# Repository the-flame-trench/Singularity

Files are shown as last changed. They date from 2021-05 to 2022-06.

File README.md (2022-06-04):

# Singularity On-board Computer
Singularity is a high-reliability focused on-board computer (OBC) for Pocketqube scale spacecraft.

It has been designed with a high degree of redundancy and fault tolerance in mind, and is compliant to ECSS-Q-ST-70-12C where possible.

# Design
The computer is based on the TI TMS570 family of safety critical microcontrollers, utilising dual lockstep ARM Cortex R4F CPU cores with extensive error checking capabilies.  

The rest of the board contains 8Mb external FRAM, 1Gb external bulk flash (both on their own single SPI bus), and a supervisor IC with RTC, watchdog and 256kb integrated FRAM (Issue_PROTO_A only).

Additionally, the board breaks out 3 CAN buses, with 1 designated for platform services, 1 for payload use, and a shared redundant bus.

As the Singularity OBC is being designed primarily for use in our TFTqube project, specific functions have been broken out to each connector, including a UART bus to a GPS module and a shared internal/external I2C bus.

The board is designed to be powered by a 3V3 external supply.  For maximum reliability, this supply should have some level of redundancy.  There is also a designated 5V input rail, although this is currently unused.

The board contains bulk decoupling for the main 3V3 rail, which is then distributed to various ICs.  The 3V3 rail is also fed through redundant TPS62850 switch mode power supplies, with outputs OR'd by an ideal diode controller and pair of MOSFETS, to provide a redundant 1V2 rail for the TMS570 core supply.

A version of the computer with 32MB SDRAM is under study, however at present, on an already dense 6 layer board, layout is infeasible.

# Usage
First, clone [TFT-KiCad-Source](https://github.com/the-flame-trench/TFT-KiCad-Source) and import all symbol and footprint libraries, found under /TFT_symbols and /TFT_footprints respectively, to your KiCad installation.  This MUST be done first, as the Singularity project references this library (as do other TFT projects).

Then, clone the Singularity repo, ensuring that your library tables are correctly set up with the TFT component libraries before opening the project.

# Contributing
The schematic and PCB are being designed in KiCad v6.0, and will move with the latest stable version.

We are working to bring every symbol and footprint into the TFT KiCad source libraries, however currently there are still a few instances using the default KiCad component library.

# Licence
Licenced under the [CERN OHLv2 - Strongly Reciprocal](LICENCE) or as referenced.

(c) The Flame Trench 2022

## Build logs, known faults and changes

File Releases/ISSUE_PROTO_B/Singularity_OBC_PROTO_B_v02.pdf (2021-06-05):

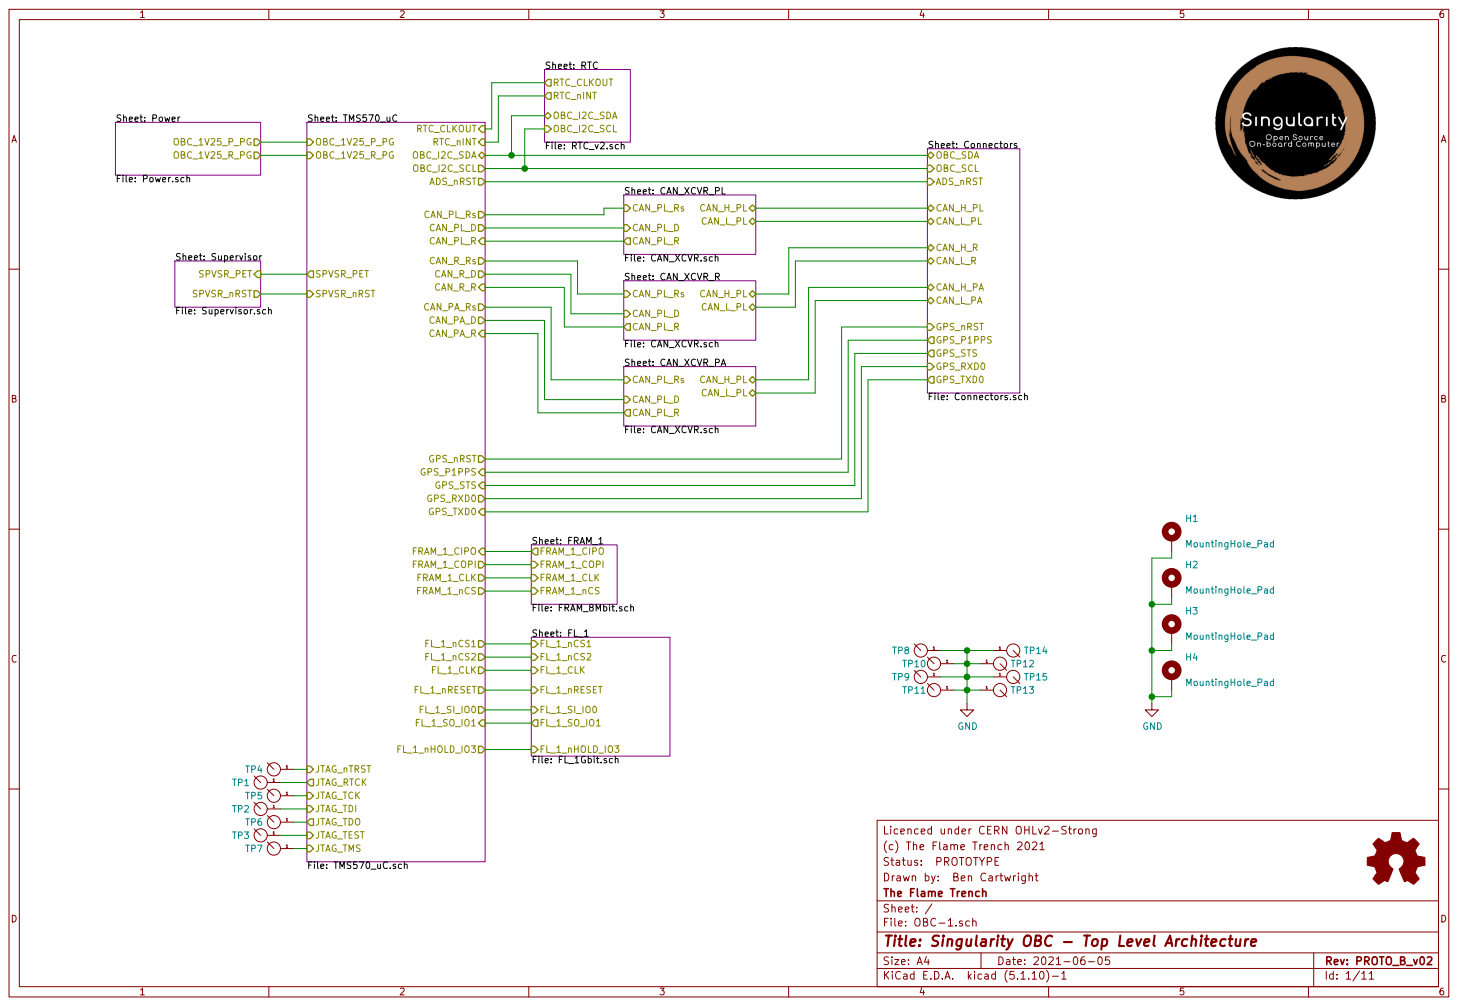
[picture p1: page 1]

File: RTC_v2.sch OBC_I2C_SDA OBC_I2C_SCL RTC_CLKOUT RTC_nINT Sheet: Power File: Power.schOBC_1V25_P_PG

Sheet: Connectors File: Connectors.sch OBC_SDA OBC_SCL ADS_nRST CAN_H_PL CAN_L_PL CAN_H_R

Licenced under CERN OHLv2-Strong
(c) The Flame Trench 2021
File: OBC-1.sch Sheet: / The Flame Trench Drawn by: Ben Cartwright Status: PROTOTYPE

Id: 1/11 Title: Singularity OBC - Top Level Architecture

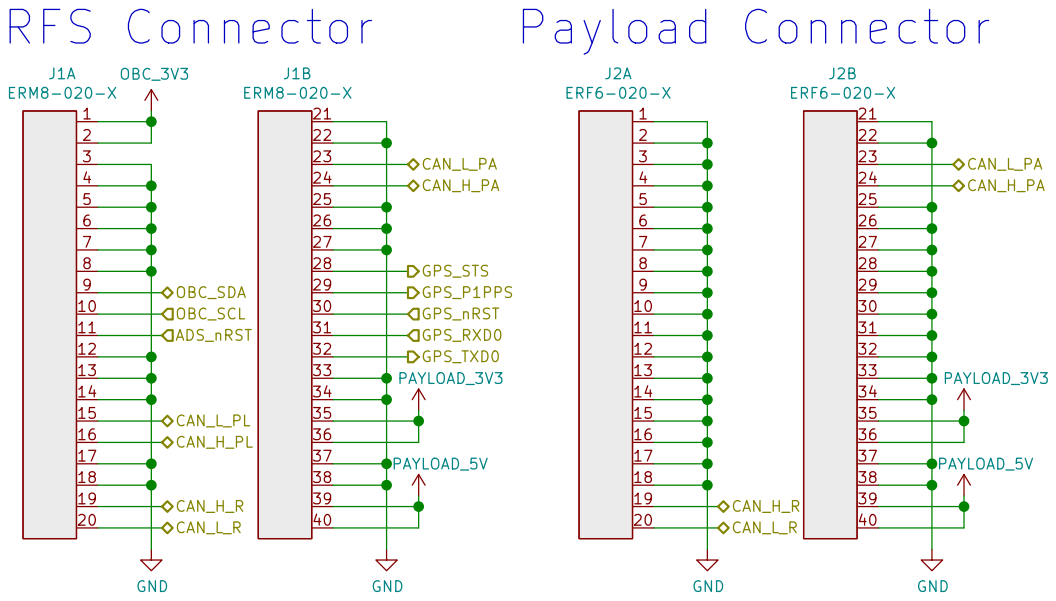
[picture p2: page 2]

Licenced under CERN OHLv2-Strong GND

(c) The Flame Trench 2021
File: Connectors.sch Sheet: /Connectors/ The Flame Trench Drawn by: Ben Cartwright Status: PROTOTYPE

Id: 2/11 Title: Singularity OBC - Connectors

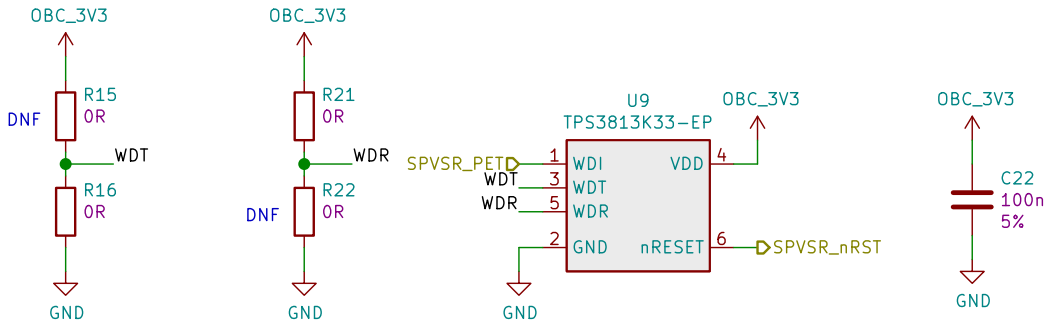
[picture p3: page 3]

Licenced under CERN OHLv2-Strong
(c) The Flame Trench 2021
Sheet: /Supervisor/ The Flame Trench Drawn by: Ben Cartwright Status: PROTOTYPE

File: Supervisor.sch
Id: 3/11 Title: Singularity OBC - Supervisor

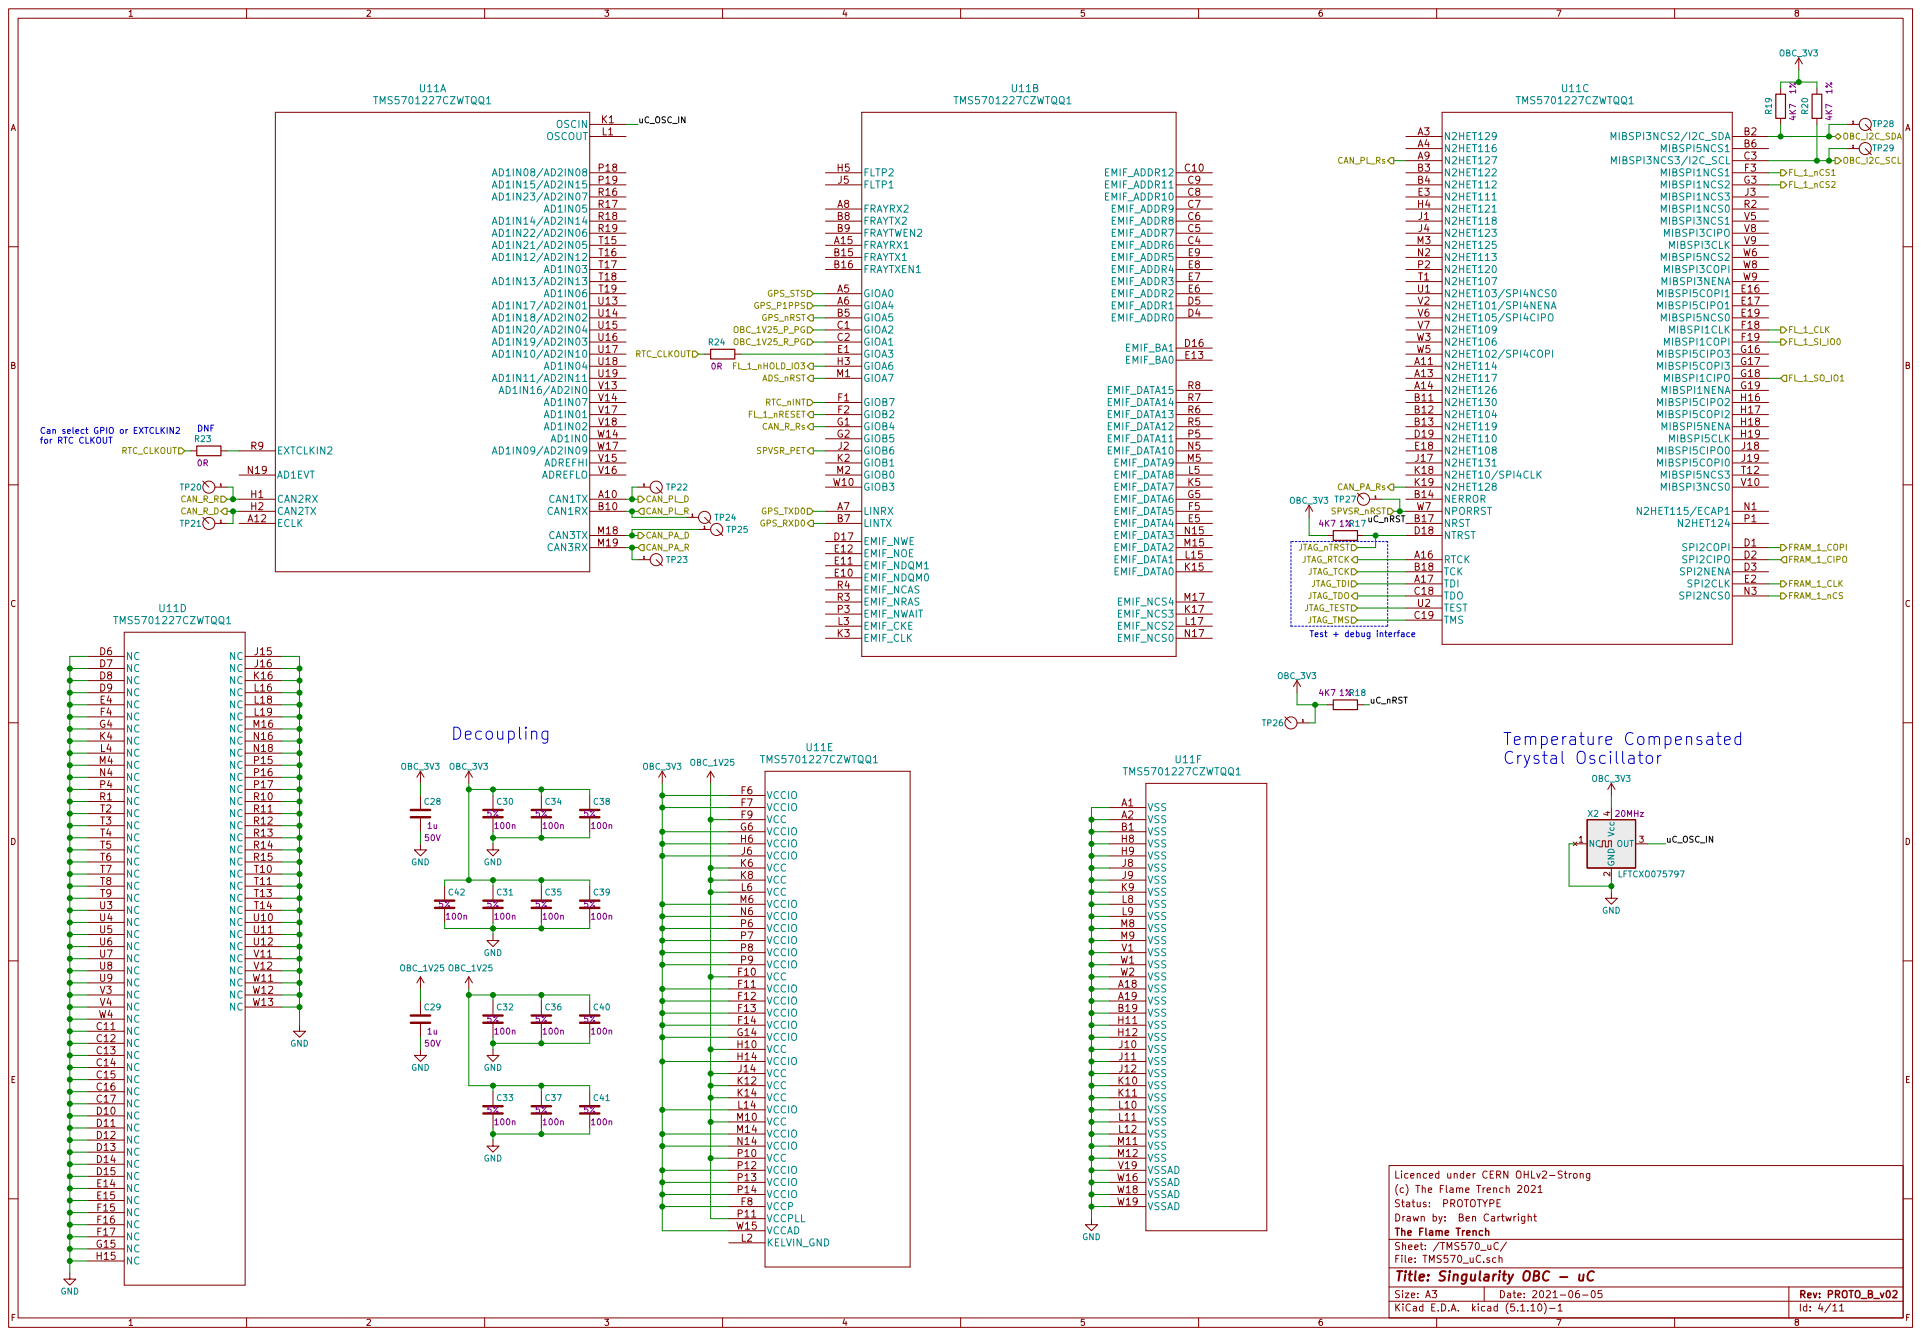
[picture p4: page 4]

Crystal Oscillator Can select GPIO or EXTCLKIN2
for RTC CLKOUT

Licenced under CERN OHLv2-Strong
(c) The Flame Trench 2021
Sheet: /TMS570_uC/ The Flame Trench Drawn by: Ben Cartwright Status: PROTOTYPE

File: TMS570_uC.sch
Id: 4/11 Title: Singularity OBC - uC

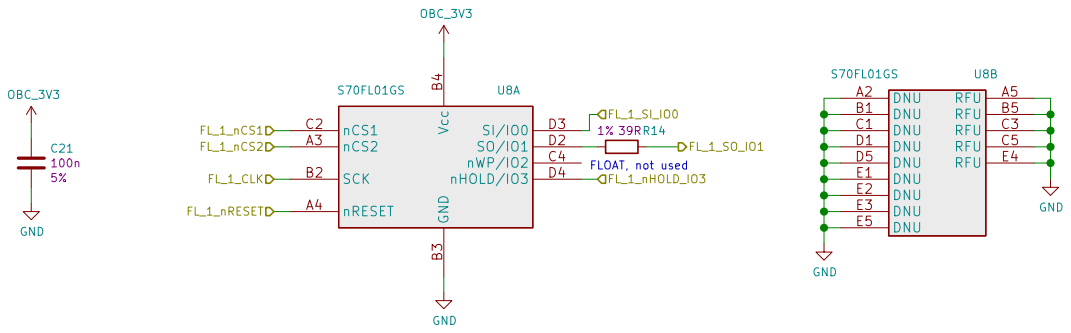
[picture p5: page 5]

Licenced under CERN OHLv2-Strong GND OBC_3V3 OBC_3V3C21

(c) The Flame Trench 2021
Sheet: /FL_1/ The Flame Trench Drawn by: Ben Cartwright Status: PROTOTYPE

File: FL_1Gbit.sch
Id: 5/11 Title: Singularity OBC - External bulk flash

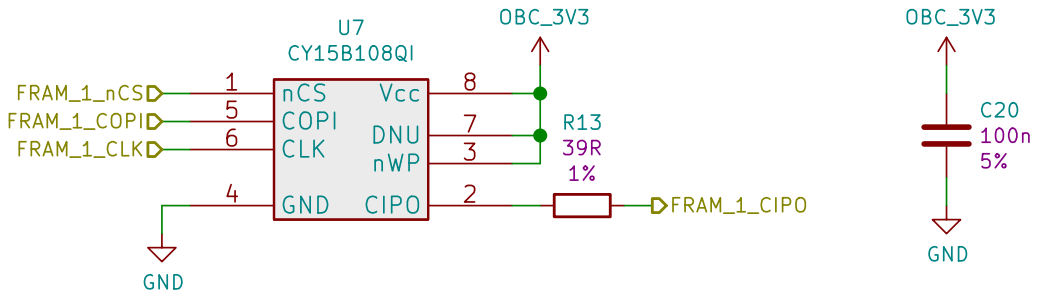
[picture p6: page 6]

Licenced under CERN OHLv2-Strong
(c) The Flame Trench 2021
Sheet: /FRAM_1/ The Flame Trench Drawn by: Ben Cartwright Status: PROTOTYPE

File: FRAM_8Mbit.sch
Id: 6/11 Title: Singularity OBC - External FRAM

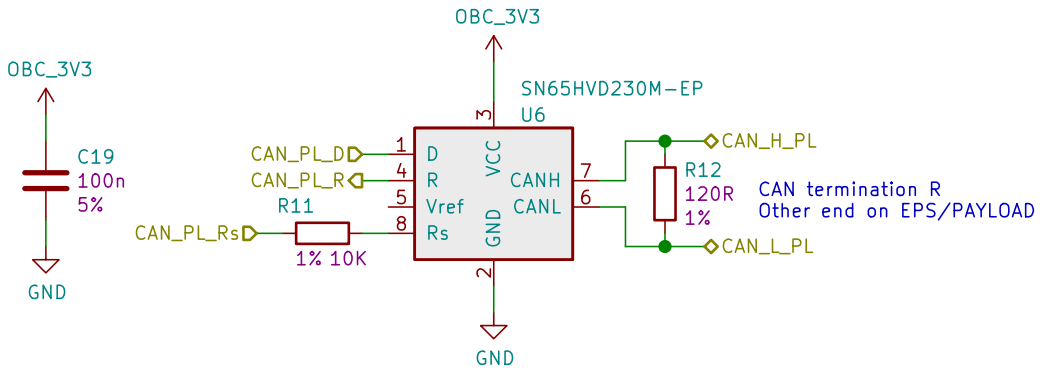
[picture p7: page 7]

Licenced under CERN OHLv2-Strong
(c) The Flame Trench 2021
Sheet: /CAN_XCVR_PA/ The Flame Trench Drawn by: Ben Cartwright Status: PROTOTYPE

File: CAN_XCVR.sch
Id: 7/11 Title: Singularity OBC - CAN Transceiver

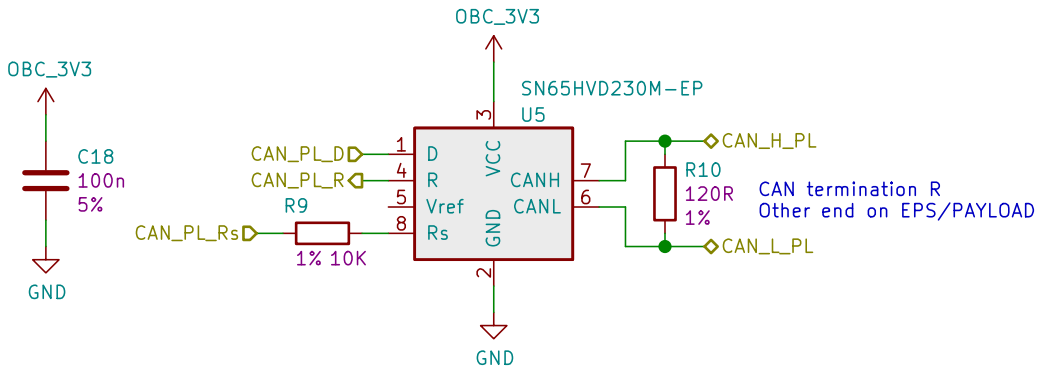
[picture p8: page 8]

Licenced under CERN OHLv2-Strong
(c) The Flame Trench 2021
Sheet: /CAN_XCVR_R/ The Flame Trench Drawn by: Ben Cartwright Status: PROTOTYPE

File: CAN_XCVR.sch
Id: 8/11 Title: Singularity OBC - CAN Transceiver

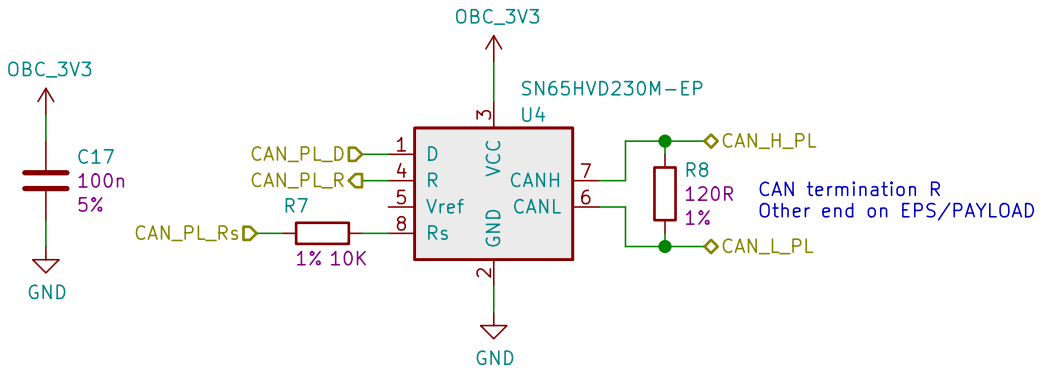
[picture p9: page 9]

Licenced under CERN OHLv2-Strong
(c) The Flame Trench 2021
Sheet: /CAN_XCVR_PL/ The Flame Trench Drawn by: Ben Cartwright Status: PROTOTYPE

File: CAN_XCVR.sch
Id: 9/11 Title: Singularity OBC - CAN Transceiver

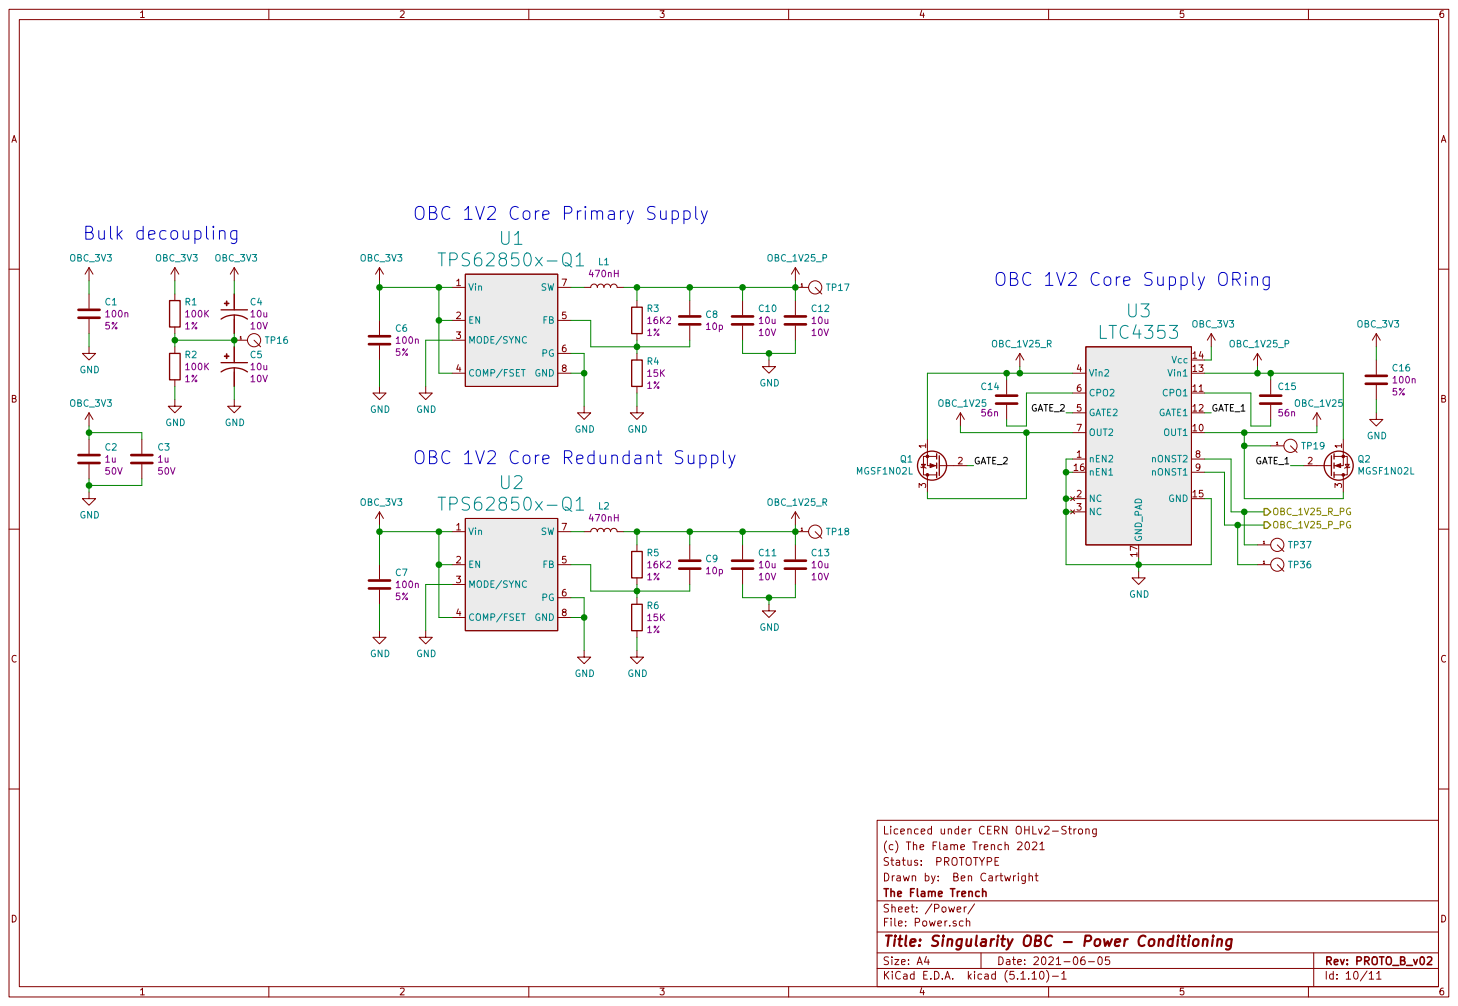
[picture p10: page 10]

OBC 1V2 Core Primary Supply

OBC 1V2 Core Redundant Supply

Licenced under CERN OHLv2-Strong C3

(c) The Flame Trench 2021
File: Power.sch Sheet: /Power/ The Flame Trench Drawn by: Ben Cartwright Status: PROTOTYPE

Id: 10/11 Title: Singularity OBC - Power Conditioning

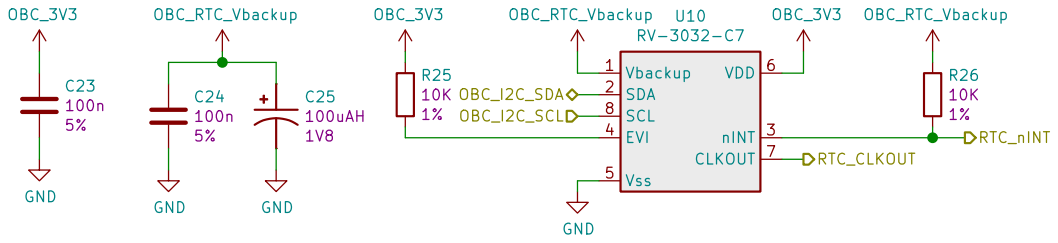
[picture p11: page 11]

Licenced under CERN OHLv2-Strong
(c) The Flame Trench 2021
File: RTC_v2.sch Sheet: /RTC/ The Flame Trench Drawn by: Ben Cartwright Status: PROTOTYPE

Id: 11/11 Title: Singularity OBC - RTC

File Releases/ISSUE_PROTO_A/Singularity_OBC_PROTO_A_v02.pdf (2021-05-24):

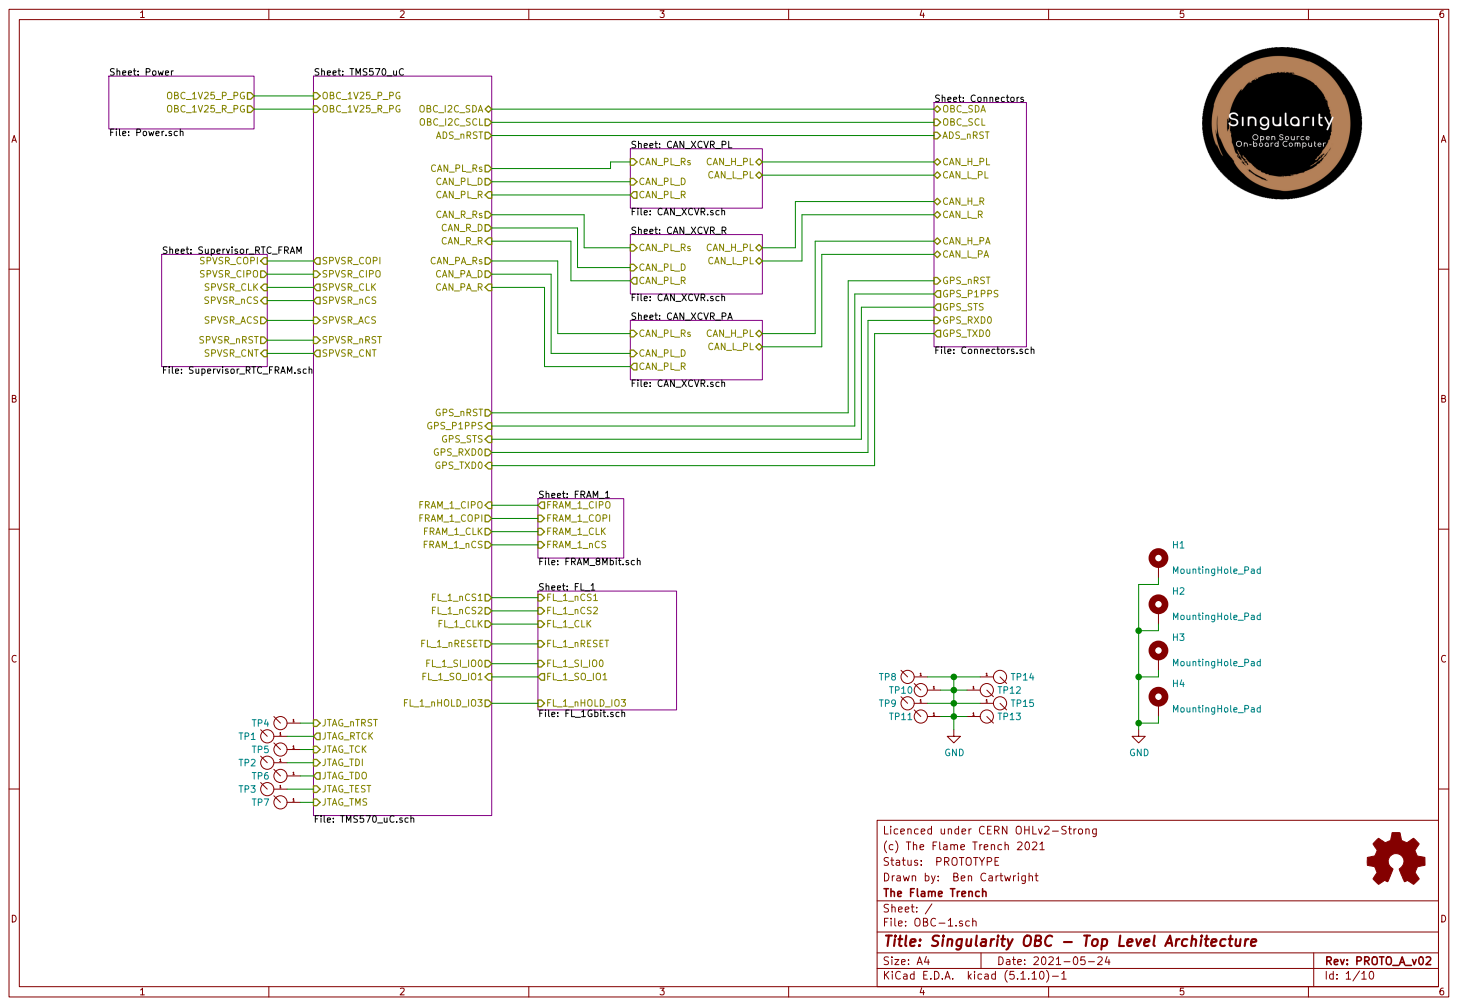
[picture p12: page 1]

Sheet: Power File: Power.schOBC_1V25_P_PG

Sheet: Connectors File: Connectors.sch OBC_SDA OBC_SCL ADS_nRST CAN_H_PL CAN_L_PL CAN_H_R

Licenced under CERN OHLv2-Strong
(c) The Flame Trench 2021
File: OBC-1.sch Sheet: / The Flame Trench Drawn by: Ben Cartwright Status: PROTOTYPE

Id: 1/10 Title: Singularity OBC - Top Level Architecture

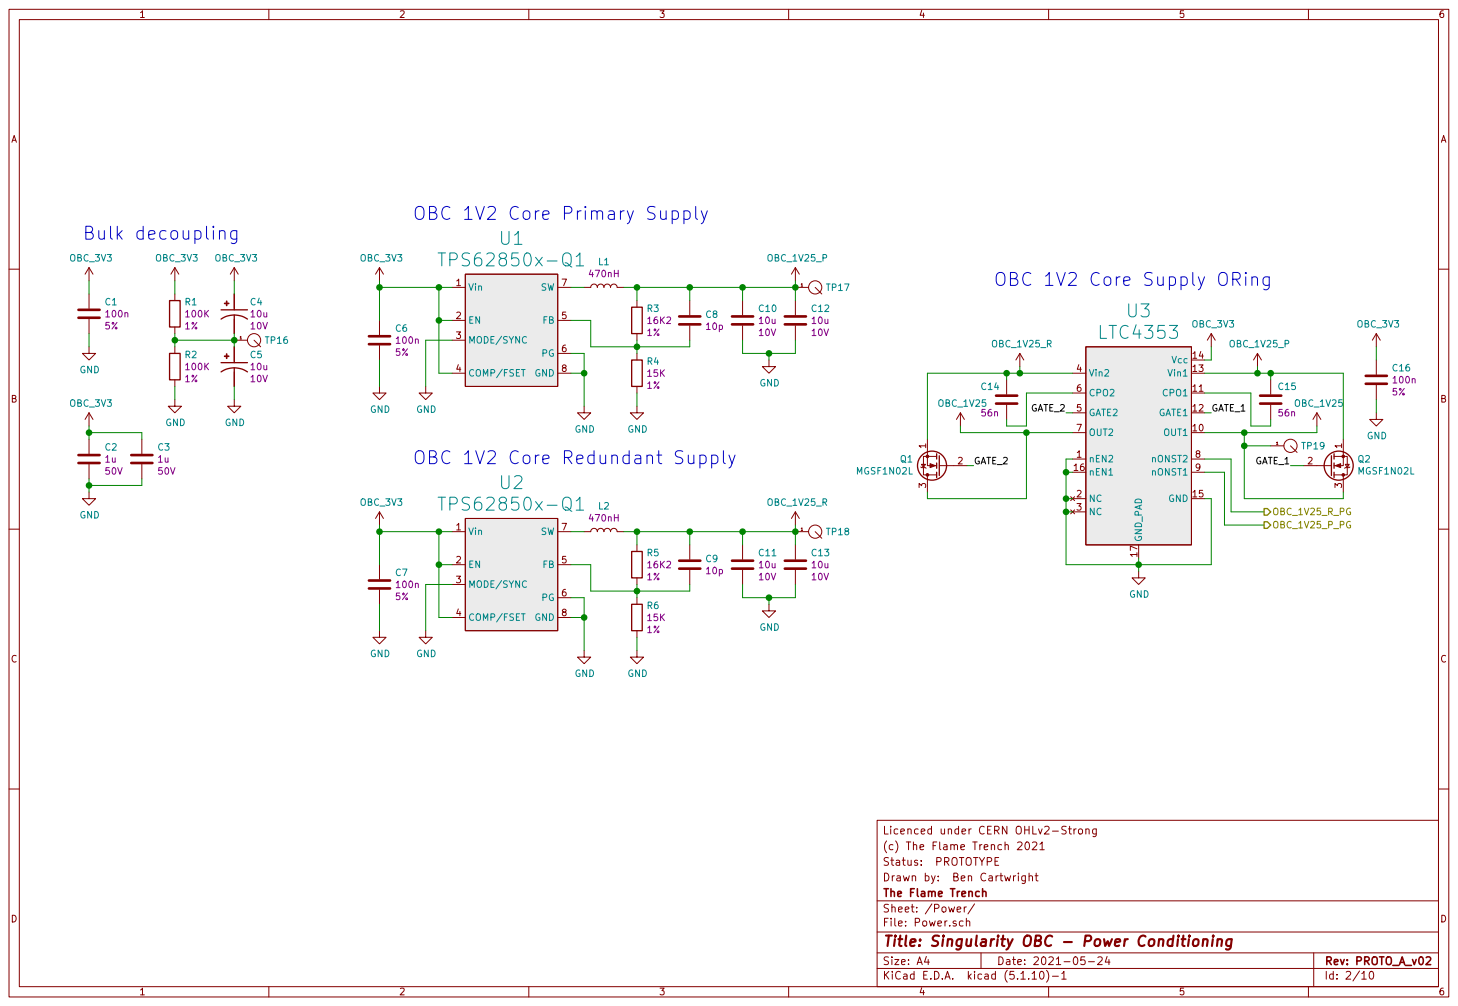
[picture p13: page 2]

OBC 1V2 Core Primary Supply

OBC 1V2 Core Supply ORing
LTC4353

OBC 1V2 Core Redundant Supply

(c) The Flame Trench 2021
File: Power.sch Sheet: /Power/ The Flame Trench Drawn by: Ben Cartwright Status: PROTOTYPE

Id: 2/10 Title: Singularity OBC - Power Conditioning


Licenced under CERN OHLv2-Strong GND

(c) The Flame Trench 2021
File: Connectors.sch Sheet: /Connectors/ The Flame Trench Drawn by: Ben Cartwright Status: PROTOTYPE

Id: 3/10 Title: Singularity OBC - Connectors


Licenced under CERN OHLv2-Strong
(c) The Flame Trench 2021
Sheet: /CAN_XCVR_PL/ The Flame Trench Drawn by: Ben Cartwright Status: PROTOTYPE

File: CAN_XCVR.sch
Id: 4/10 Title: Singularity OBC - CAN Transceiver


Licenced under CERN OHLv2-Strong
(c) The Flame Trench 2021
Sheet: /CAN_XCVR_R/ The Flame Trench Drawn by: Ben Cartwright Status: PROTOTYPE

File: CAN_XCVR.sch
Id: 5/10 Title: Singularity OBC - CAN Transceiver


Licenced under CERN OHLv2-Strong
(c) The Flame Trench 2021
Sheet: /CAN_XCVR_PA/ The Flame Trench Drawn by: Ben Cartwright Status: PROTOTYPE

File: CAN_XCVR.sch
Id: 6/10 Title: Singularity OBC - CAN Transceiver


Licenced under CERN OHLv2-Strong
(c) The Flame Trench 2021
Sheet: /FRAM_1/ The Flame Trench Drawn by: Ben Cartwright Status: PROTOTYPE

File: FRAM_8Mbit.sch
Id: 7/10 Title: Singularity OBC - External FRAM


Licenced under CERN OHLv2-Strong GND OBC_3V3 OBC_3V3C21

(c) The Flame Trench 2021
Sheet: /FL_1/ The Flame Trench Drawn by: Ben Cartwright Status: PROTOTYPE

File: FL_1Gbit.sch
Id: 8/10 Title: Singularity OBC - External bulk flash

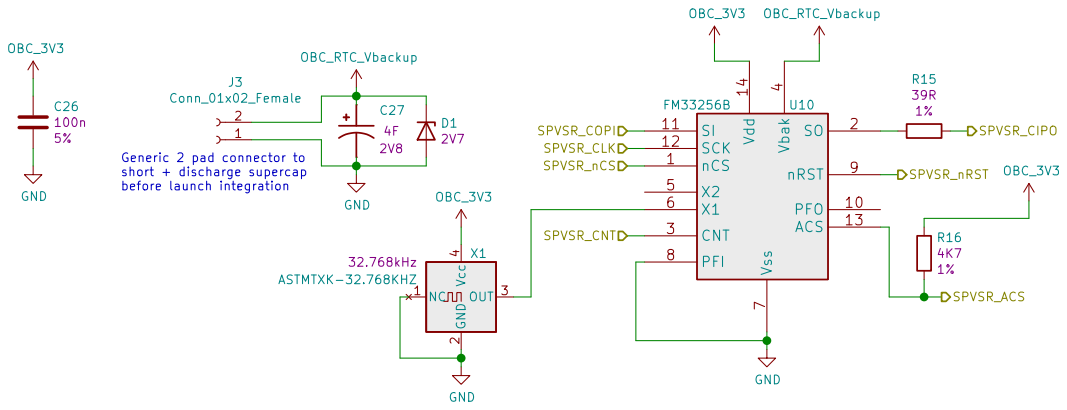
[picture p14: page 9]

SPVSR_nRST SPVSR_ACS Generic 2 pad connector to
short + discharge supercap
before launch integration

Licenced under CERN OHLv2-Strong
(c) The Flame Trench 2021
Sheet: /Supervisor_RTC_FRAM/ The Flame Trench Drawn by: Ben Cartwright Status: PROTOTYPE

File: Supervisor_RTC_FRAM.sch
Id: 9/10 Title: Singularity OBC - uC Supervisor + RTC

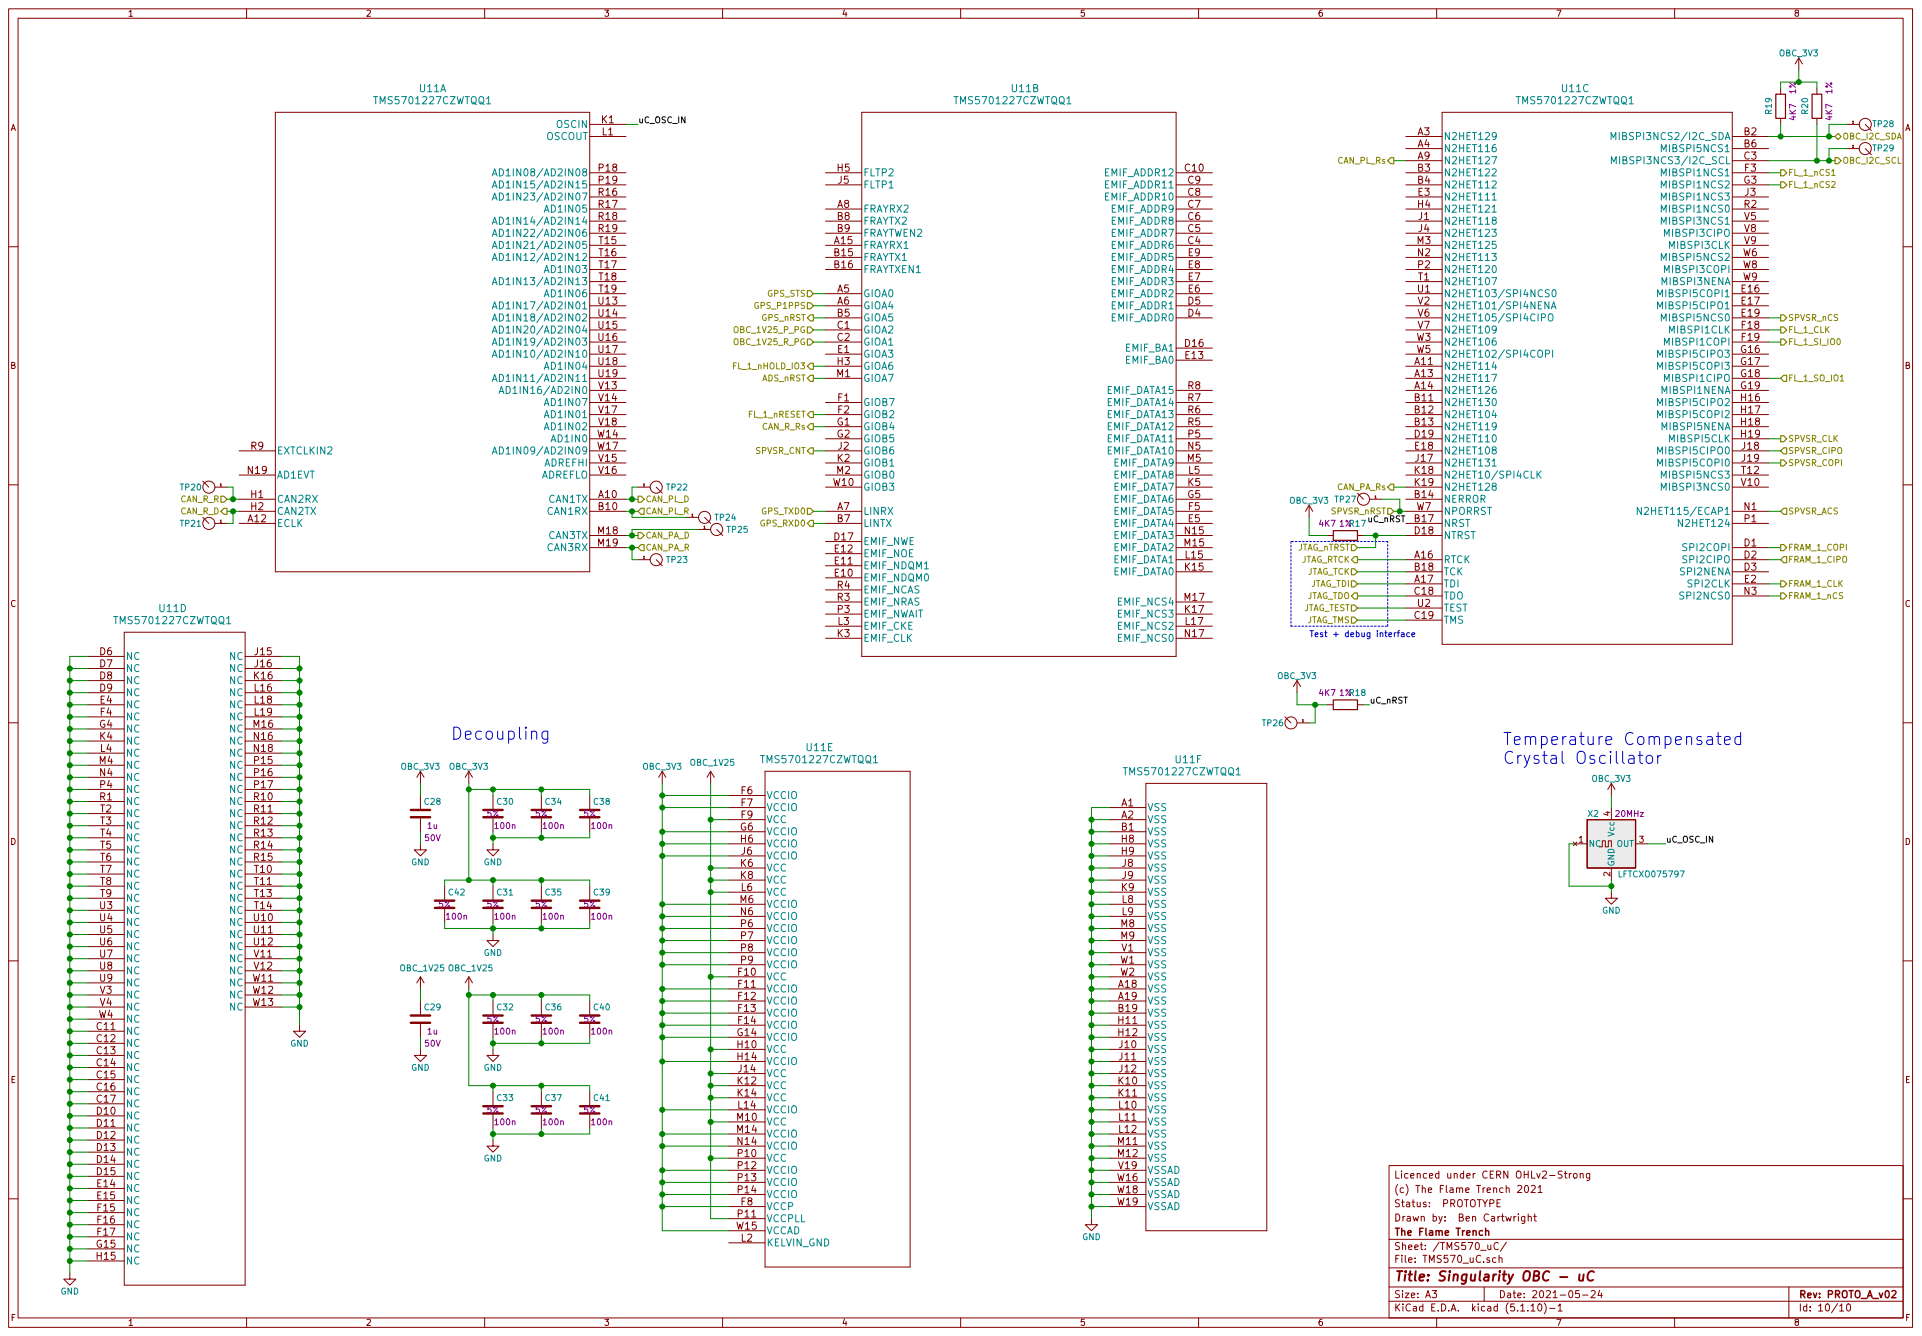
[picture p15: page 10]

Licenced under CERN OHLv2-Strong
(c) The Flame Trench 2021
Sheet: /TMS570_uC/ The Flame Trench Drawn by: Ben Cartwright Status: PROTOTYPE

File: TMS570_uC.sch
Id: 10/10 Title: Singularity OBC - uC

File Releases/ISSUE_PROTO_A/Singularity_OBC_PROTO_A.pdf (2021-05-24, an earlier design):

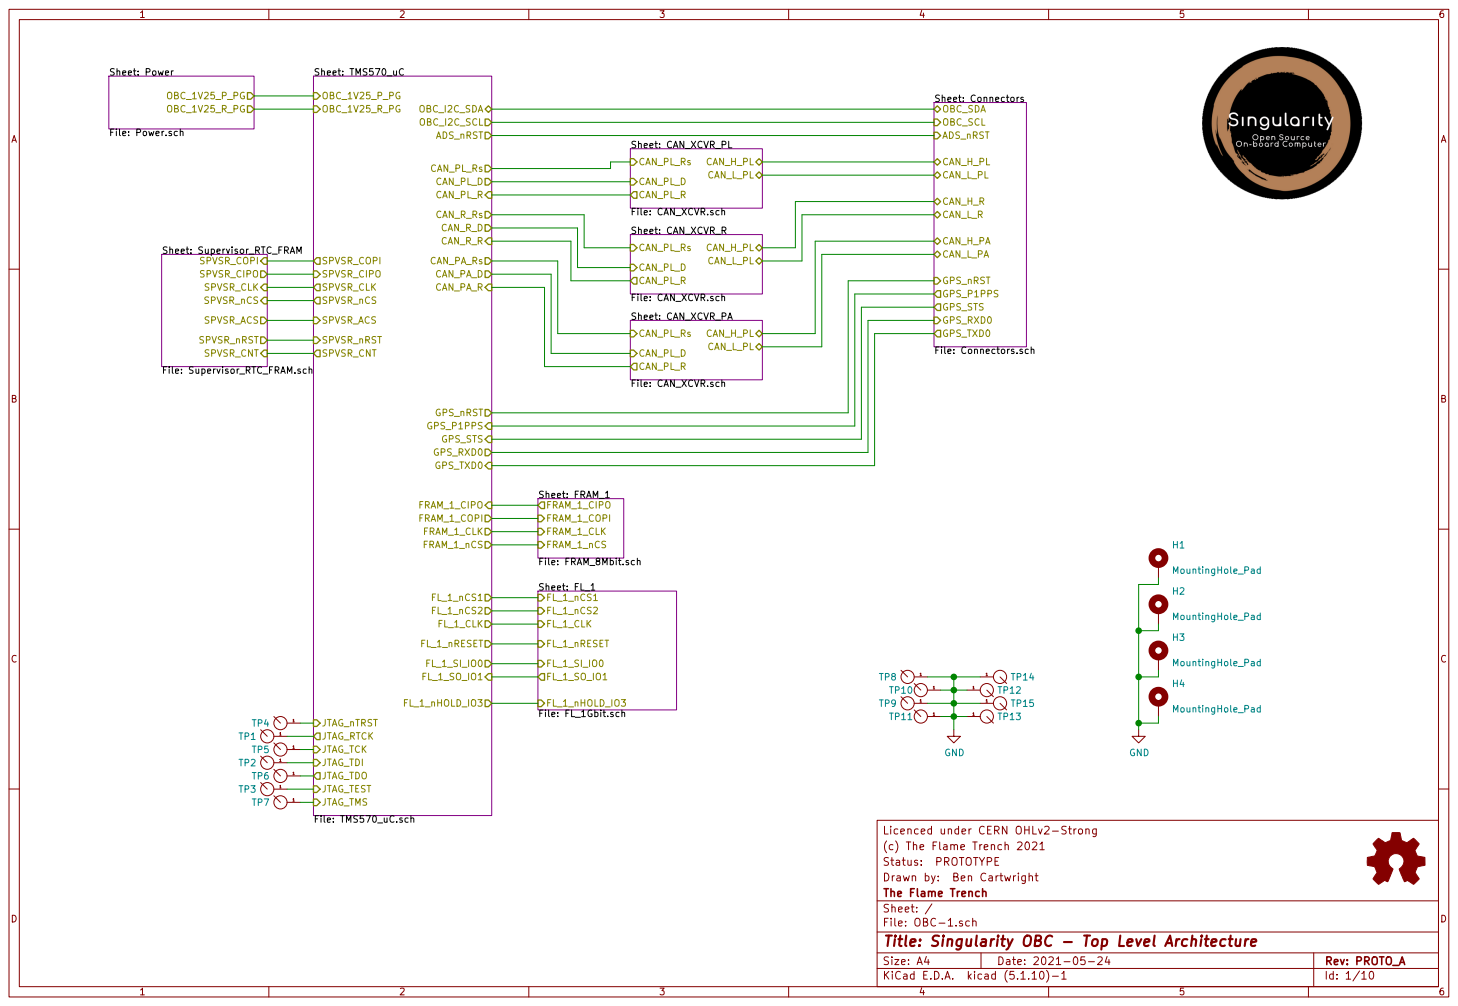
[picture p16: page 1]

Sheet: Power File: Power.schOBC_1V25_P_PG

Sheet: Connectors File: Connectors.sch OBC_SDA OBC_SCL ADS_nRST CAN_H_PL CAN_L_PL CAN_H_R

Licenced under CERN OHLv2-Strong
(c) The Flame Trench 2021
File: OBC-1.sch Sheet: / The Flame Trench Drawn by: Ben Cartwright Status: PROTOTYPE

Id: 1/10 Title: Singularity OBC - Top Level Architecture

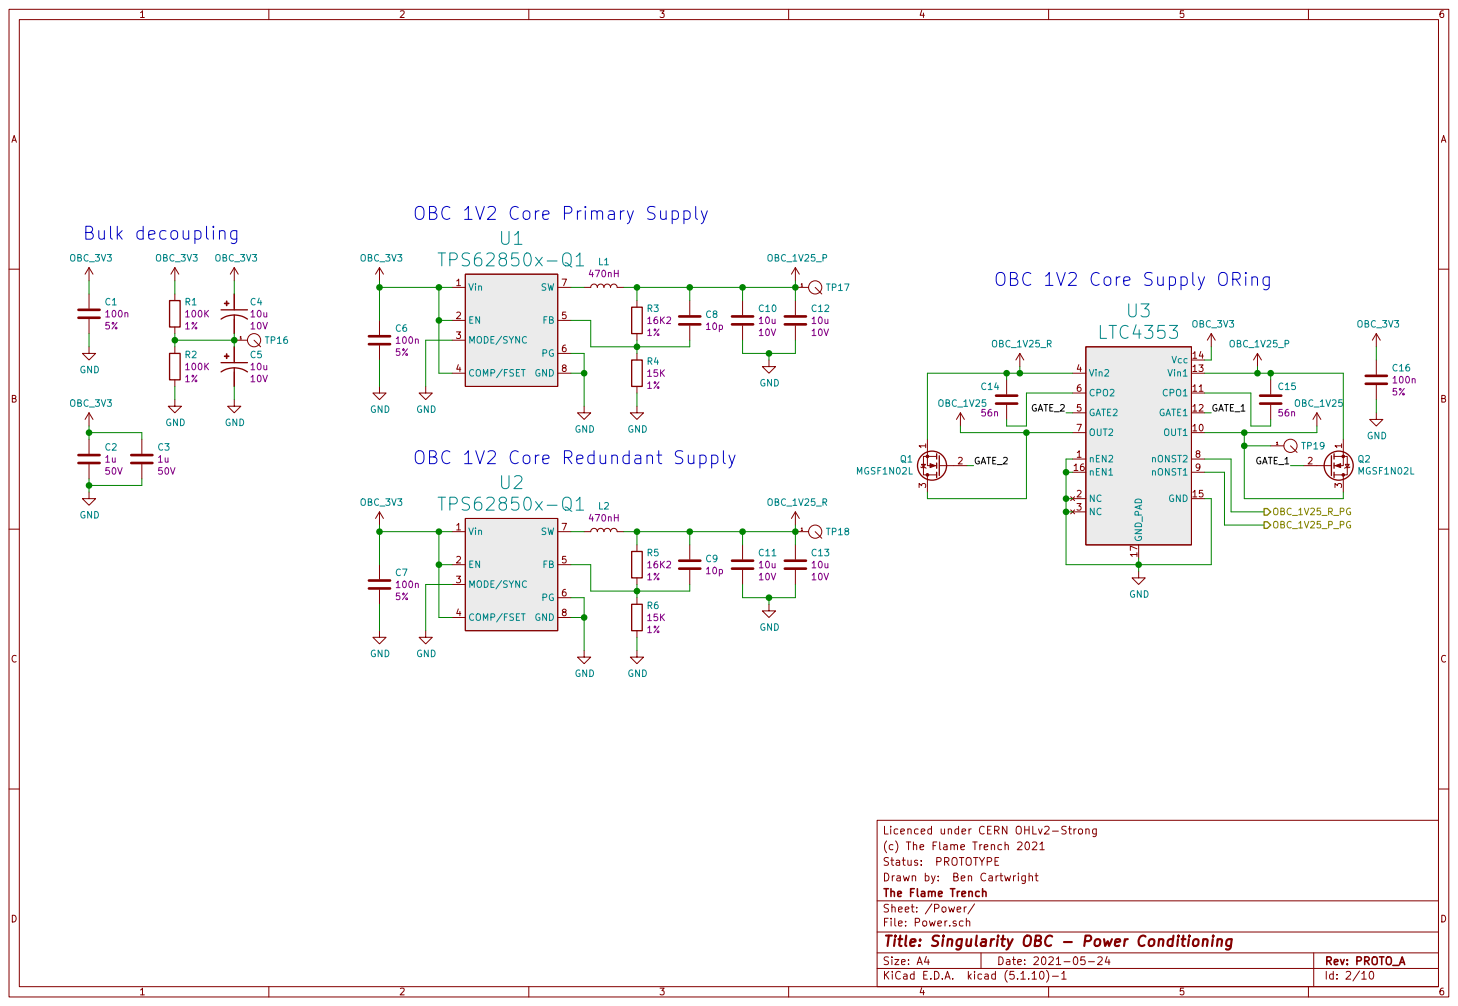
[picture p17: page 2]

OBC 1V2 Core Primary Supply

OBC 1V2 Core Supply ORing
LTC4353

OBC 1V2 Core Redundant Supply

(c) The Flame Trench 2021
File: Power.sch Sheet: /Power/ The Flame Trench Drawn by: Ben Cartwright Status: PROTOTYPE

Id: 2/10 Title: Singularity OBC - Power Conditioning


Licenced under CERN OHLv2-Strong GND

(c) The Flame Trench 2021
File: Connectors.sch Sheet: /Connectors/ The Flame Trench Drawn by: Ben Cartwright Status: PROTOTYPE

Id: 3/10 Title: Singularity OBC - Connectors


Licenced under CERN OHLv2-Strong
(c) The Flame Trench 2021
Sheet: /CAN_XCVR_PL/ The Flame Trench Drawn by: Ben Cartwright Status: PROTOTYPE

File: CAN_XCVR.sch
Id: 4/10 Title: Singularity OBC - CAN Transceiver


Licenced under CERN OHLv2-Strong
(c) The Flame Trench 2021
Sheet: /CAN_XCVR_R/ The Flame Trench Drawn by: Ben Cartwright Status: PROTOTYPE

File: CAN_XCVR.sch
Id: 5/10 Title: Singularity OBC - CAN Transceiver


Licenced under CERN OHLv2-Strong
(c) The Flame Trench 2021
Sheet: /CAN_XCVR_PA/ The Flame Trench Drawn by: Ben Cartwright Status: PROTOTYPE

File: CAN_XCVR.sch
Id: 6/10 Title: Singularity OBC - CAN Transceiver


Licenced under CERN OHLv2-Strong
(c) The Flame Trench 2021
Sheet: /FRAM_1/ The Flame Trench Drawn by: Ben Cartwright Status: PROTOTYPE

File: FRAM_8Mbit.sch
Id: 7/10 Title: Singularity OBC - External FRAM


Licenced under CERN OHLv2-Strong GND OBC_3V3 OBC_3V3C21

(c) The Flame Trench 2021
Sheet: /FL_1/ The Flame Trench Drawn by: Ben Cartwright Status: PROTOTYPE

File: FL_1Gbit.sch
Id: 8/10 Title: Singularity OBC - External bulk flash


SPVSR_nRST SPVSR_ACS Generic 2 pad connector to
short + discharge supercap
before launch integration

Licenced under CERN OHLv2-Strong
(c) The Flame Trench 2021
Sheet: /Supervisor_RTC_FRAM/ The Flame Trench Drawn by: Ben Cartwright Status: PROTOTYPE

File: Supervisor_RTC_FRAM.sch
Id: 9/10 Title: Singularity OBC - uC Supervisor + RTC

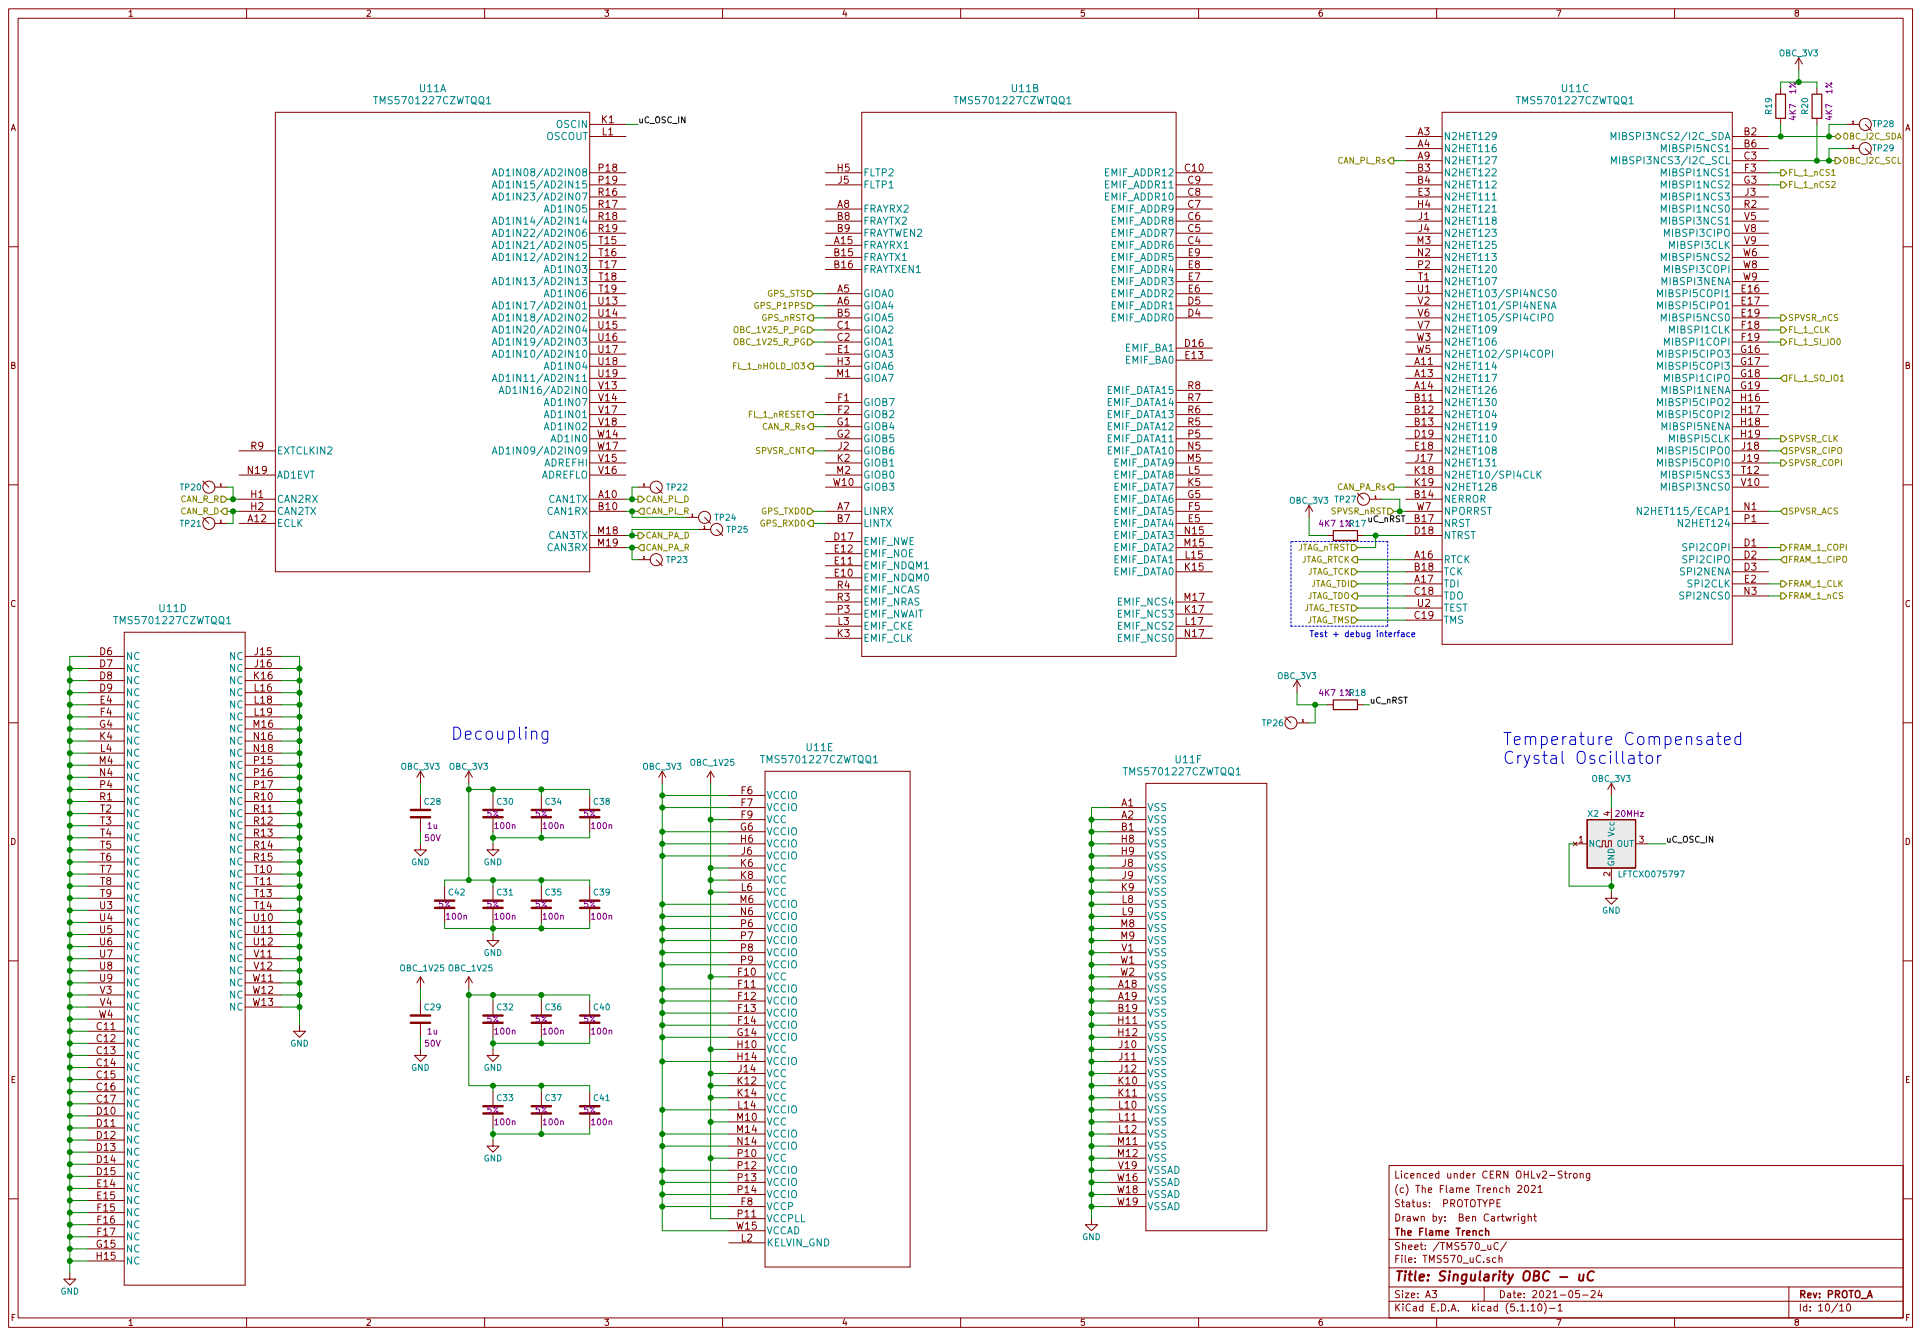
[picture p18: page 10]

(c) The Flame Trench 2021
Sheet: /TMS570_uC/ The Flame Trench Drawn by: Ben Cartwright Status: PROTOTYPE

File: TMS570_uC.sch
Id: 10/10 Title: Singularity OBC - uC

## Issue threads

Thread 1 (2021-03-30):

Update OBC_1V2 to 1.25V

TFT-Ben, 2021-03-30:
Update all the power nets from OBC_1V2 to OBC_1V25.  This purposeful slight overvolting is to compensate for Rds losses through the power ORing MOSFETs at high current loads in the TMS570 core.

TFT-Ben, 2021-03-30:
Power symbol has been updated

TFT-Ben, 2021-03-30:
Schematic updated to reflect new regulator configuration

Closed 2021-03-30.

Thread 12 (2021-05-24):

Temperature sensor

TFT-Ben, 2021-05-24:
Would probably be worth it to implement a small I2C based temperature sensor IC next to the TMS570

TFT-Ben, 2021-09-24:
Implemented in Issue Proto B v03

Closed 2021-09-24.

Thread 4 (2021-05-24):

Change testpoints to through-hole type

TFT-Ben, 2021-05-24:
Test points, at least GND test points, should be TH/via type to allow for smaller pogo pin/bed-of-nails testpoint alignment

Closed 2021-10-01.

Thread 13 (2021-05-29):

Add test point to OBC_1V25 net on IssB + BoN

TFT-Ben, 2021-05-29:
OBC_1V25_P/R nets have test points, but no inherent way of verifying that the ORing circuitry is working as the output is not probed.

Test points for OBC_1V25_P_PG and OBC_1V25_R_PG might also be useful?

TFT-Ben, 2021-05-29:
Workflow should be to add test point to both schematics, then the computer PCB - note the PCB testpoint location (or copy the PCB files across to the BoN if the layout for that hasn't been started) and ensure the BoN test point is in the same position.
TP footprint on BoN will be manually changed to a PTH suitable for pogo pin soldering

TFT-Ben, 2021-05-29:
Test points added to schematic in BoN branch

TFT-Ben, 2021-05-29:
Make sure these have the same ref_des in the computer schematic vs the BoN!

TFT-Ben, 2021-06-05:
These TPs have been added to schematic, need implementing on PCB

TFT-Ben, 2021-06-05:
Test points implemented on Issue_PROTO_B_v002

Closed 2021-06-05.

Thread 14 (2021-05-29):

Test points for FRAM, RTC_v2, Flash, CAN XCVRs?

TFT-Ben, 2021-05-29:
CAN has pre-driver R/D lines test pointed through the TMS570 sch (fix?)
Other modules are pretty thin on the ground wrt test points, add later

TFT-Ben, 2021-05-29:
CAN_H/L test points for all 3 buses added at top level

TFT-Ben, 2021-06-05:
CAN_H/L test points marked for removal, using connector passthrough instead.  Other modules (FRAM, RTC_v2, flash) may need probing in the future

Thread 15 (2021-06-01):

Update BoM and generate parts price list

TFT-Ben, 2021-06-01:
HTML BoM export needs updating for Issue_PROTO_B, and a parts list with prices should be generated with quotes for runs for 10-25 boards.  Include suppliers and generate procurement lists by supplier.

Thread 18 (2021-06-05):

Add title to RTC_v2 schematic in Issue_PROTO_B

TFT-Ben, 2021-06-05:

Closed 2021-06-05.

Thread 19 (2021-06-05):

Add JTAG connector to BoN

TFT-Ben, 2021-06-05:
Check ATMEL-ICE user guide for correct connector and pinout

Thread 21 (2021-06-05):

Connect SPVSR_nRST pin in BoN schematic

TFT-Ben, 2021-06-05:
Pin is broken out from TMS570 sch but not connected to EGSE connector

Closed 2021-06-05.

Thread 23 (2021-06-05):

Remove test points from BoN schematics

TFT-Ben, 2021-06-05:
As these are connector signal passthroughs, remove test points and reserve in case test points are added to Singularity board in the future for:
TP16
TP19
TP30
TP31
TP32
TP33
TP34

TFT-Ben, 2021-06-05:
Also rename TP35 in BoN to TP19

Closed 2021-06-05.

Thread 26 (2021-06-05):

Add ATSAME and USB interface to Issue B BoN board

TFT-Ben, 2021-06-05:
Active CAN programming and testing uC needs adding to EGSE board, with USB interface and implementing CAN_PL and CAN_R buses, as well as any relevant voltage checks in the ADC

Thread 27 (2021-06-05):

Review Issue_B test point refdes before doing BoN PCB layout

TFT-Ben, 2021-06-05:
Ensure test point refdes are up to date and identical, to make sure that the pogo pin locations remain the same and refer to the same net, copying across the most recent Issue B PCB (should be design locked) before beginning layout of the BoN card.

TFT-Ben, 2022-06-04:
IssB PCB has been copied across to BoN project, needs checking and extraneous components removing.

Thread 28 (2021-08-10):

OR-ing supply MOSFET drain-source resistance changes with temperature

manaljosid, 2021-08-10:
The temperature effects on drain-source resistance in the OR-ing supply need to be taken into account in power budgeting

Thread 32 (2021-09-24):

Bed of Nails board file to be recopied

abhignay, 2021-09-24:
The position of TP15 (GND) and TP27 (Supervisor chips rst) has been changed in Singularity Proto v03 to make room for the new temperature sensor, so the Bed of Nails pogo pin file should be recopied.

Closed 2021-10-01.

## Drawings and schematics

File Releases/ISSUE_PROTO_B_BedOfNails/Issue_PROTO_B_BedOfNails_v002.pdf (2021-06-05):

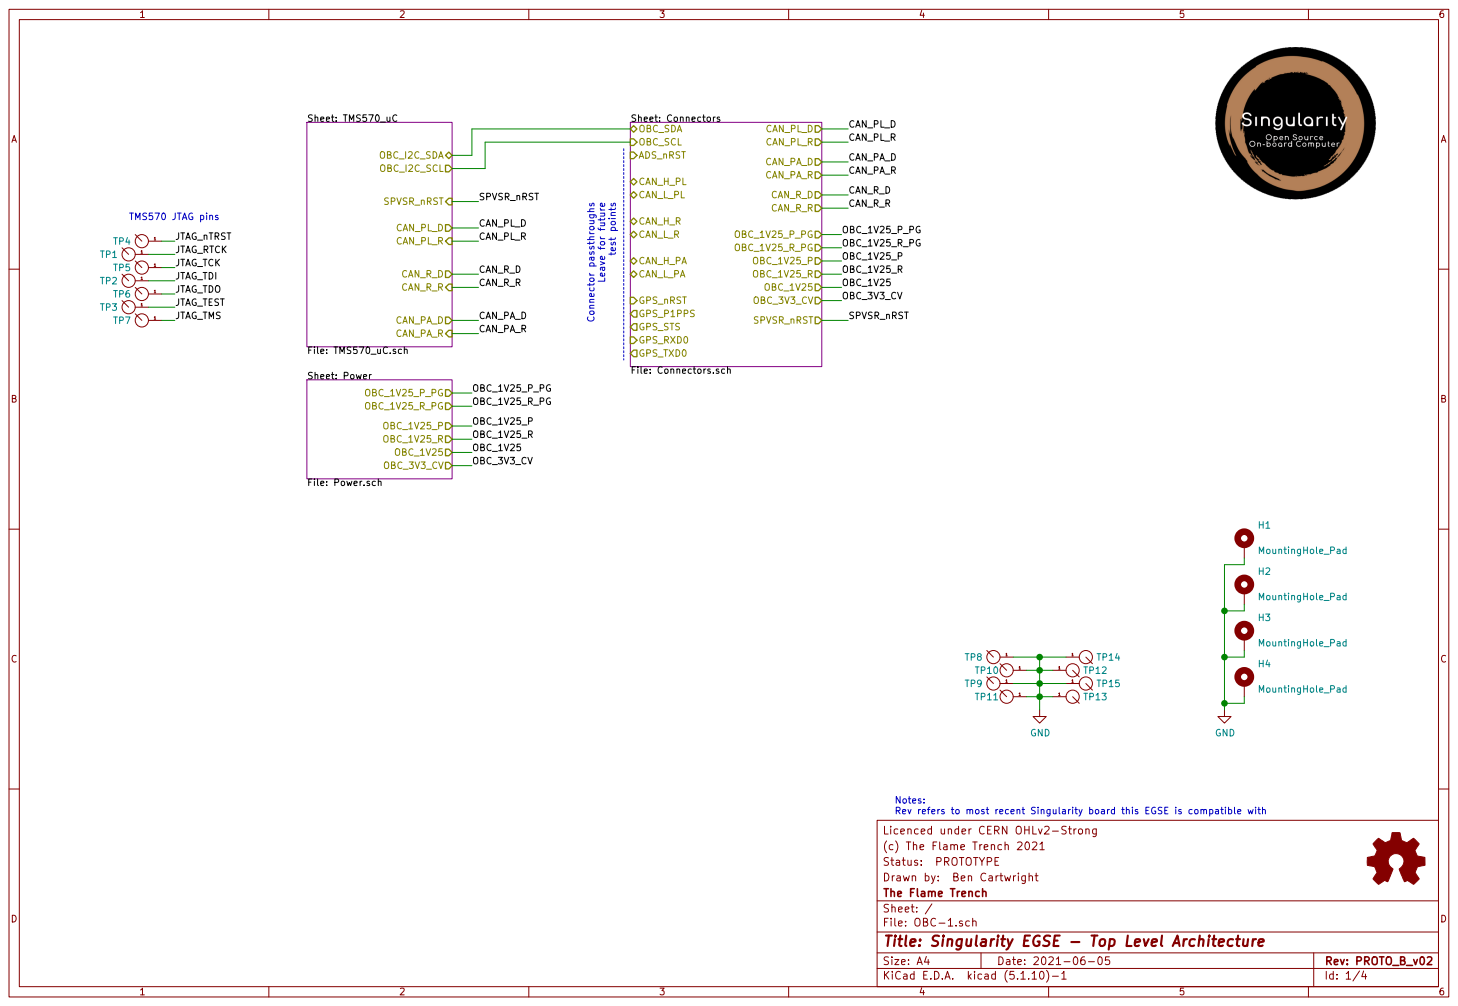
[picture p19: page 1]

CAN_PA_R OBC_I2C_SDA OBC_I2C_SCL SPVSR_nRST Sheet: Power File: Power.schOBC_1V25_P_PG

Sheet: Connectors File: Connectors.sch OBC_SDA OBC_SCL ADS_nRST CAN_H_PL CAN_L_PL CAN_H_R

Notes: Rev refers to most recent Singularity board this EGSE is compatible with

Licenced under CERN OHLv2-Strong
(c) The Flame Trench 2021
File: OBC-1.sch Sheet: / The Flame Trench Drawn by: Ben Cartwright Status: PROTOTYPE

Id: 1/4 Title: Singularity EGSE - Top Level Architecture

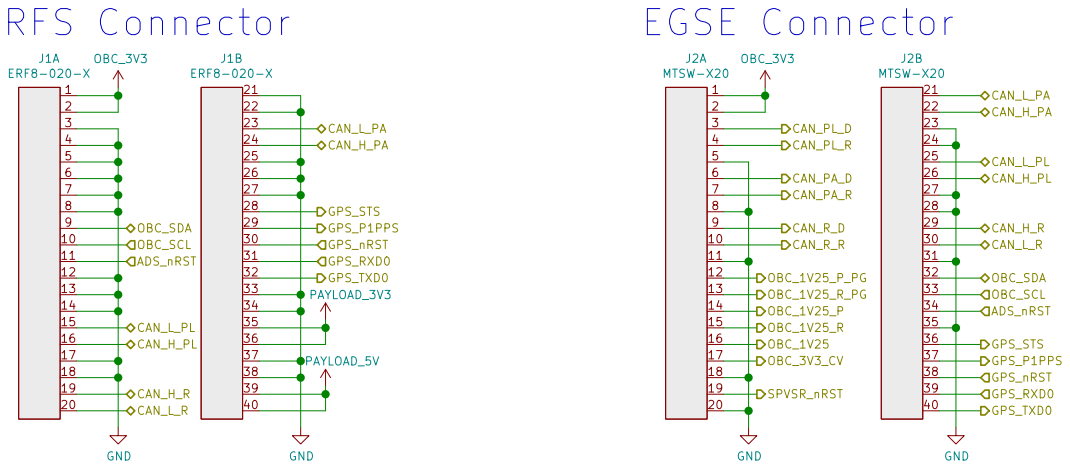
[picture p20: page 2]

Licenced under CERN OHLv2-Strong
(c) The Flame Trench 2021
File: Connectors.sch Sheet: /Connectors/ The Flame Trench Drawn by: Ben Cartwright Status: PROTOTYPE

Id: 2/4 Title: Singularity EGSE - Connectors

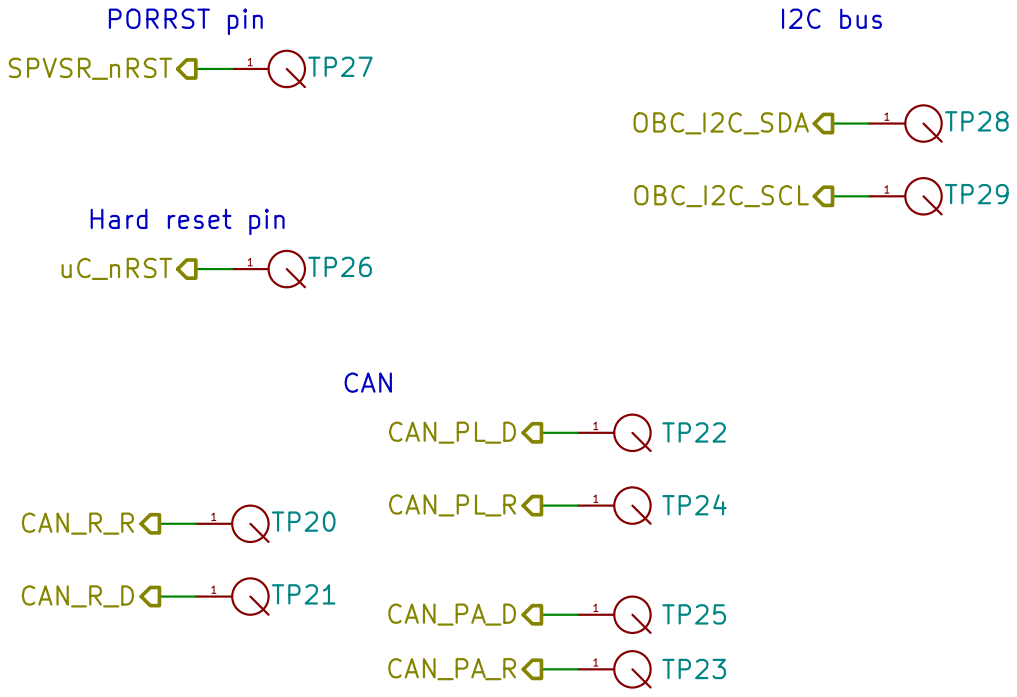
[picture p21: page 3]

I2C bus Hard reset pin

Licenced under CERN OHLv2-Strong
(c) The Flame Trench 2021
Sheet: /TMS570_uC/ The Flame Trench Drawn by: Ben Cartwright Status: PROTOTYPE

File: TMS570_uC.sch
Id: 3/4 Title: Singularity EGSE - uC

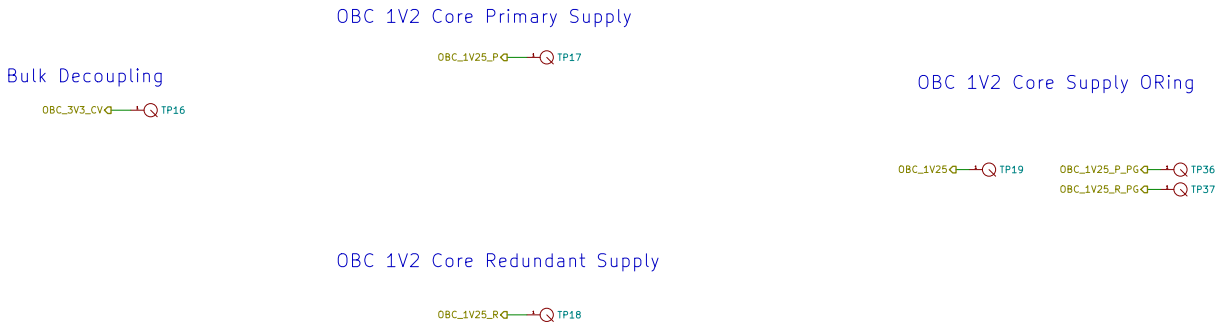
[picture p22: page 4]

OBC 1V2 Core Redundant Supply

Licenced under CERN OHLv2-Strong
(c) The Flame Trench 2021
File: Power.sch Sheet: /Power/ The Flame Trench Drawn by: Ben Cartwright Status: PROTOTYPE

Id: 4/4 Title: Singularity EGSE - Power Conditioning

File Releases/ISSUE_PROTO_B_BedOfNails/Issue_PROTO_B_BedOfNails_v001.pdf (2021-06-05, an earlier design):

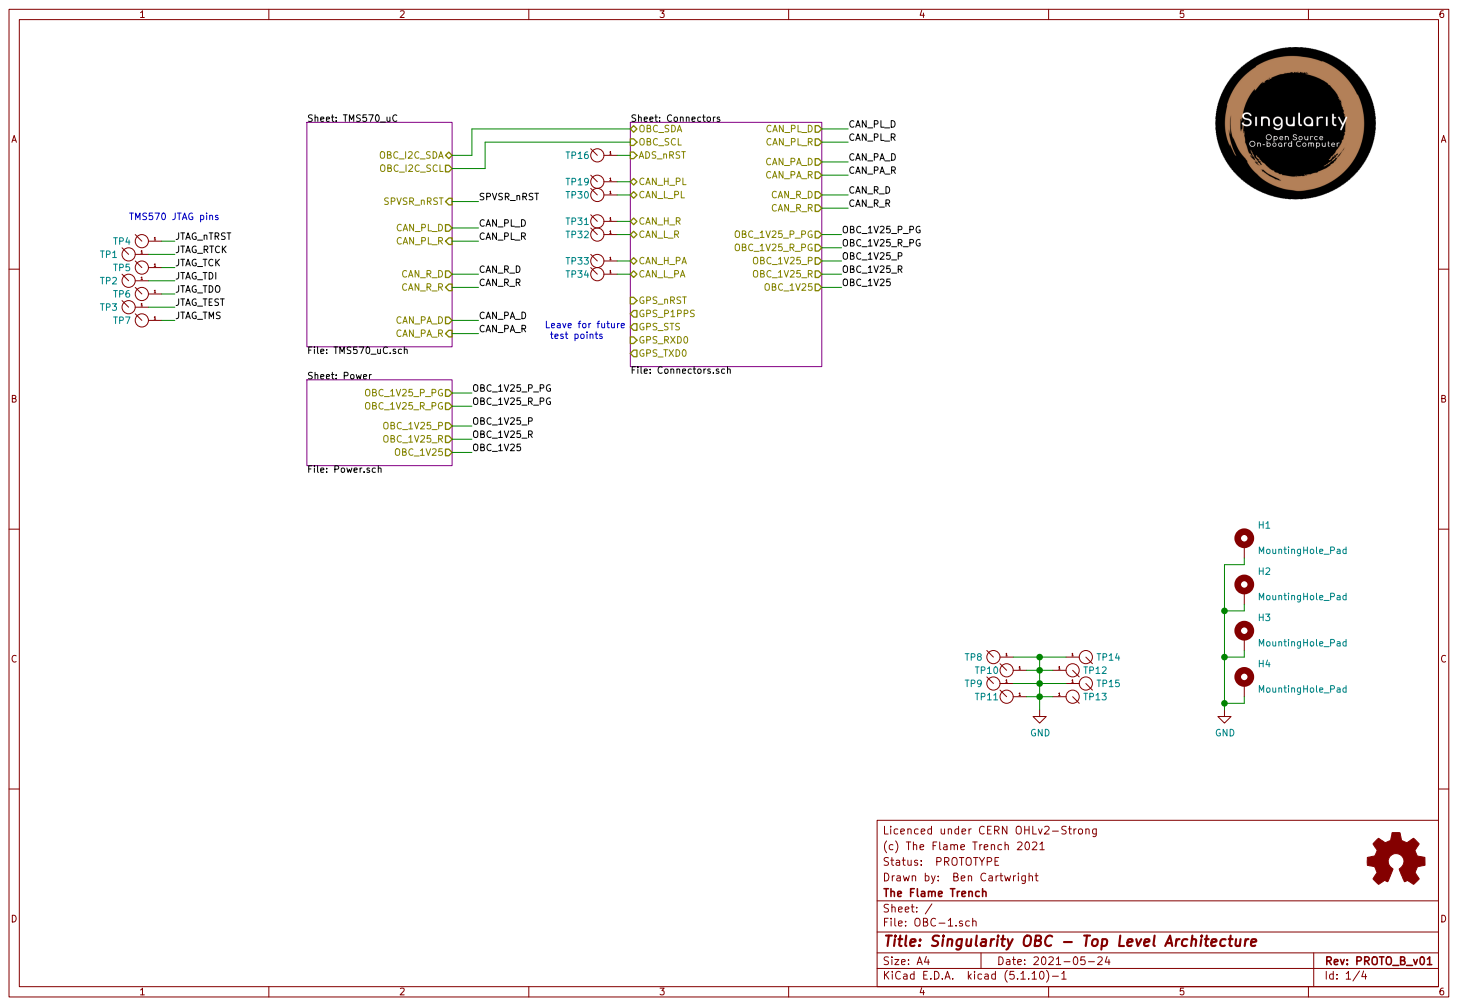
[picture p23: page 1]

CAN_PA_R OBC_I2C_SDA OBC_I2C_SCL SPVSR_nRST Sheet: Power File: Power.schOBC_1V25_P_PG

Licenced under CERN OHLv2-Strong
(c) The Flame Trench 2021
File: OBC-1.sch Sheet: / The Flame Trench Drawn by: Ben Cartwright Status: PROTOTYPE

Id: 1/4 Title: Singularity OBC - Top Level Architecture

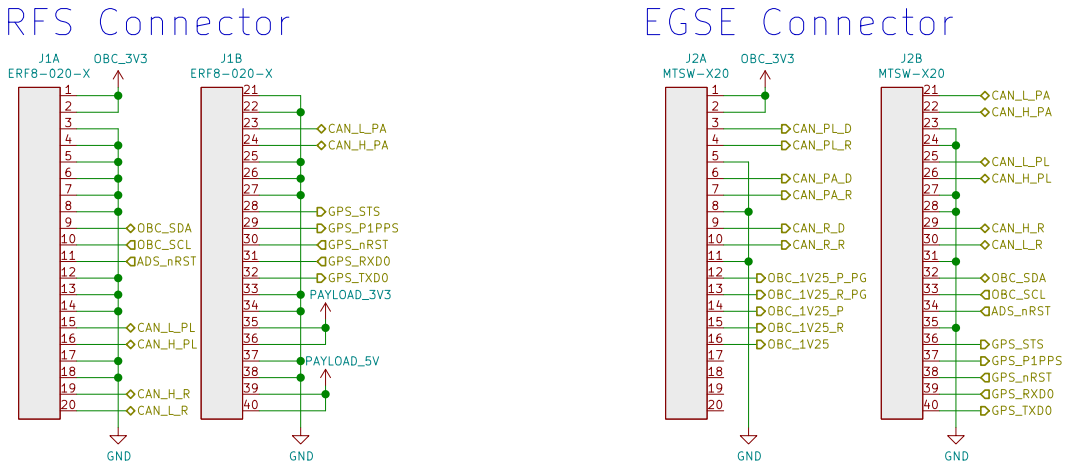
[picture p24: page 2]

Licenced under CERN OHLv2-Strong
(c) The Flame Trench 2021
File: Connectors.sch Sheet: /Connectors/ The Flame Trench Drawn by: Ben Cartwright Status: PROTOTYPE

Id: 2/4 Title: Singularity OBC - Connectors


I2C bus Hard reset pin

Licenced under CERN OHLv2-Strong
(c) The Flame Trench 2021
Sheet: /TMS570_uC/ The Flame Trench Drawn by: Ben Cartwright Status: PROTOTYPE

File: TMS570_uC.sch
Id: 3/4 Title: Singularity OBC - uC

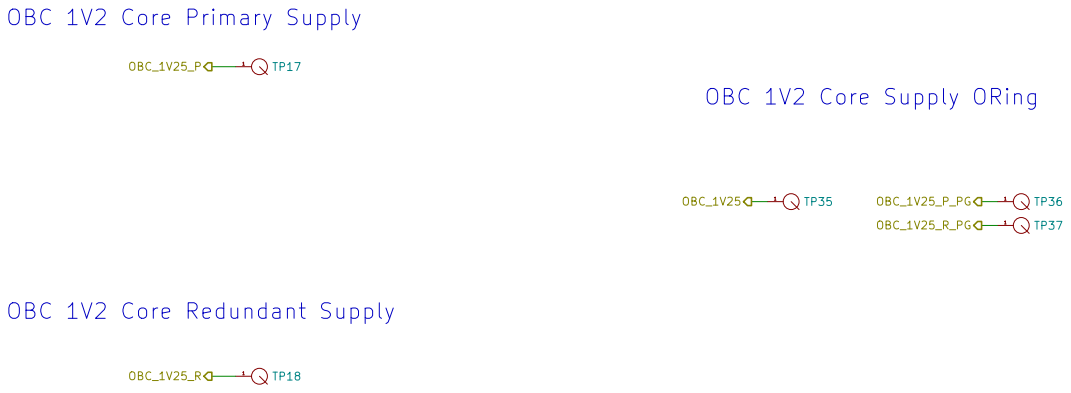
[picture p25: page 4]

OBC_1V25 OBC 1V2 Core Primary Supply

OBC 1V2 Core Supply ORing

OBC 1V2 Core Redundant Supply

Licenced under CERN OHLv2-Strong
(c) The Flame Trench 2021
File: Power.sch Sheet: /Power/ The Flame Trench Drawn by: Ben Cartwright Status: PROTOTYPE

Id: 4/4 Title: Singularity OBC - Power Conditioning

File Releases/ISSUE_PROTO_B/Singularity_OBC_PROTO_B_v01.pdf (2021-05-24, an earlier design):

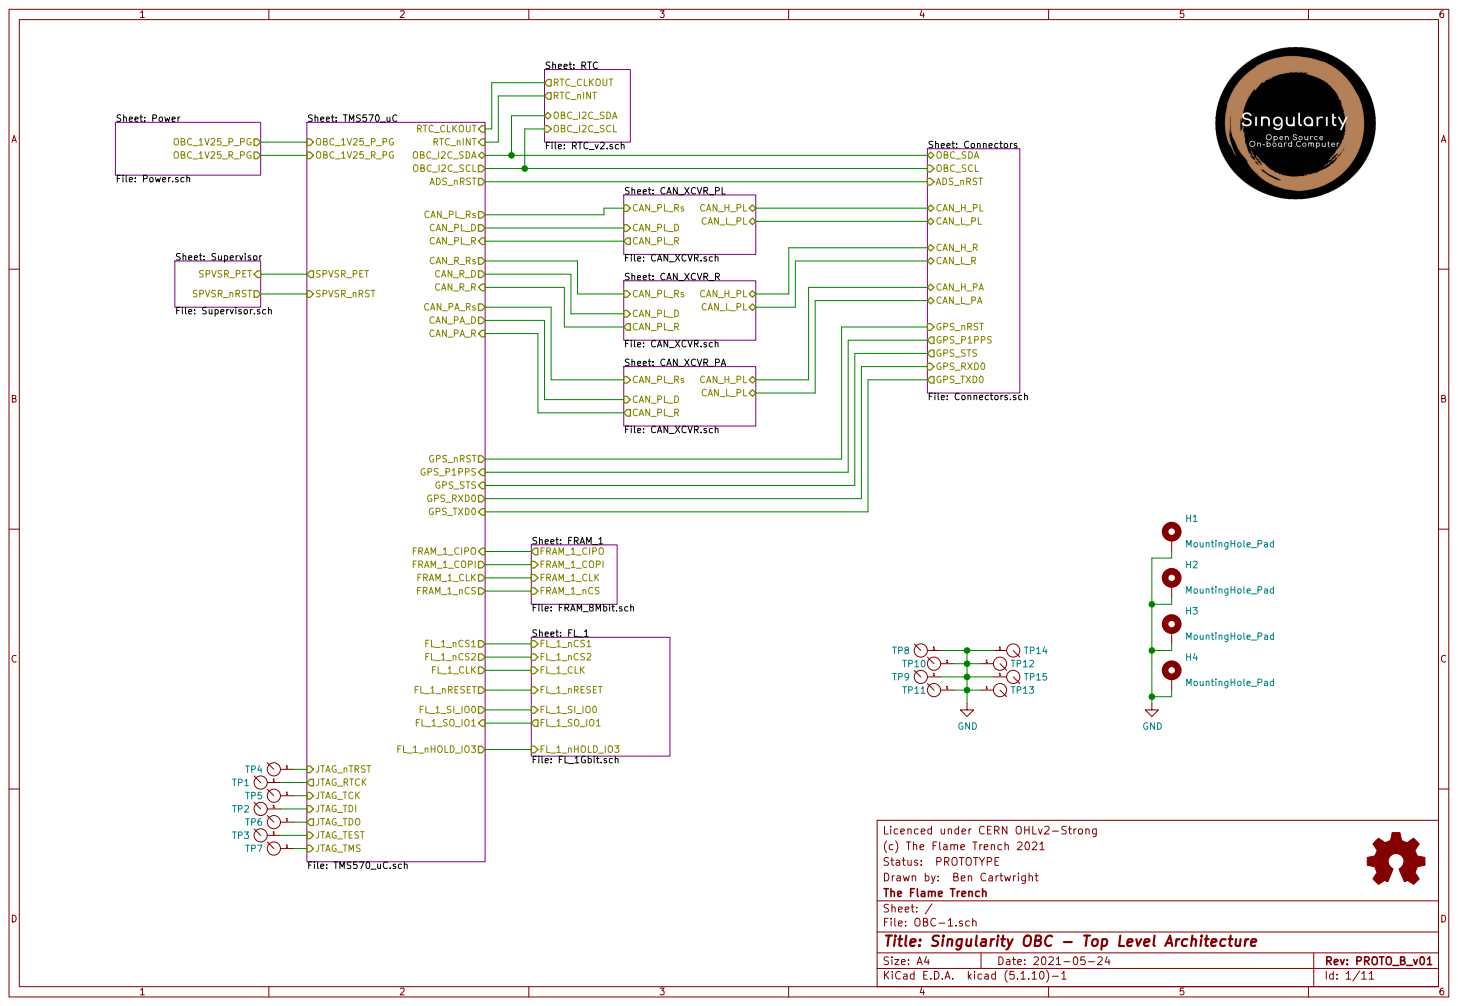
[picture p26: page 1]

Sheet: Power File: Power.schOBC_1V25_P_PG

Sheet: Connectors File: Connectors.sch OBC_SDA OBC_SCL ADS_nRST CAN_H_PL CAN_L_PL CAN_H_R

Licenced under CERN OHLv2-Strong
(c) The Flame Trench 2021
File: OBC-1.sch Sheet: / The Flame Trench Drawn by: Ben Cartwright Status: PROTOTYPE

Id: 1/11 Title: Singularity OBC - Top Level Architecture


Licenced under CERN OHLv2-Strong GND

(c) The Flame Trench 2021
File: Connectors.sch Sheet: /Connectors/ The Flame Trench Drawn by: Ben Cartwright Status: PROTOTYPE

Id: 2/11 Title: Singularity OBC - Connectors


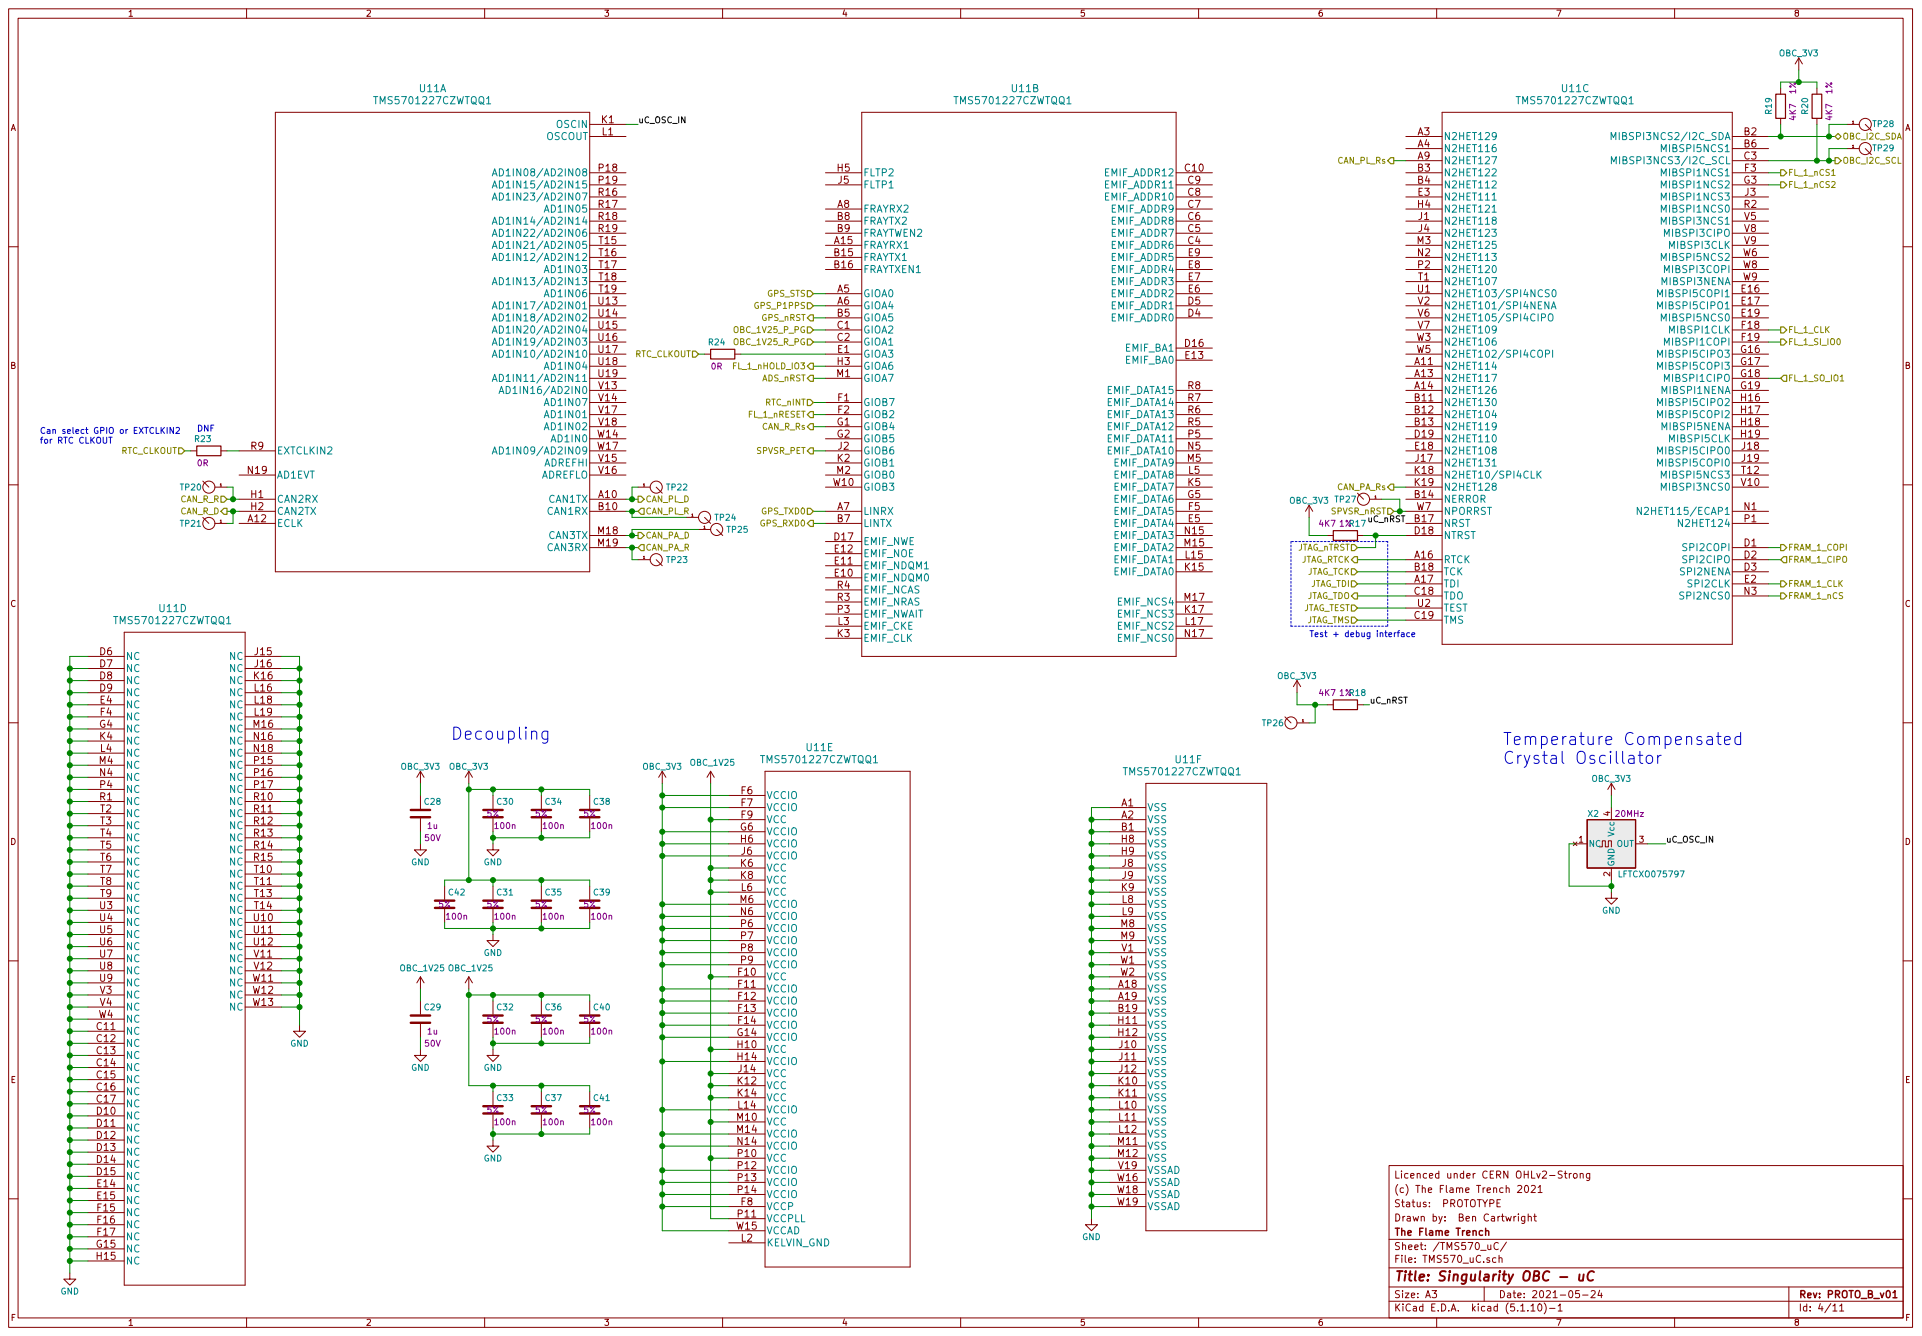
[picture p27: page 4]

Crystal Oscillator Can select GPIO or EXTCLKIN2
for RTC CLKOUT

Licenced under CERN OHLv2-Strong
(c) The Flame Trench 2021
Sheet: /TMS570_uC/ The Flame Trench Drawn by: Ben Cartwright Status: PROTOTYPE

File: TMS570_uC.sch
Id: 4/11 Title: Singularity OBC - uC


Licenced under CERN OHLv2-Strong GND OBC_3V3 OBC_3V3C21

(c) The Flame Trench 2021
Sheet: /FL_1/ The Flame Trench Drawn by: Ben Cartwright Status: PROTOTYPE

File: FL_1Gbit.sch
Id: 5/11 Title: Singularity OBC - External bulk flash


Licenced under CERN OHLv2-Strong
(c) The Flame Trench 2021
Sheet: /FRAM_1/ The Flame Trench Drawn by: Ben Cartwright Status: PROTOTYPE

File: FRAM_8Mbit.sch
Id: 6/11 Title: Singularity OBC - External FRAM


Licenced under CERN OHLv2-Strong
(c) The Flame Trench 2021
Sheet: /CAN_XCVR_PA/ The Flame Trench Drawn by: Ben Cartwright Status: PROTOTYPE

File: CAN_XCVR.sch
Id: 7/11 Title: Singularity OBC - CAN Transceiver


Licenced under CERN OHLv2-Strong
(c) The Flame Trench 2021
Sheet: /CAN_XCVR_R/ The Flame Trench Drawn by: Ben Cartwright Status: PROTOTYPE

File: CAN_XCVR.sch
Id: 8/11 Title: Singularity OBC - CAN Transceiver


Licenced under CERN OHLv2-Strong
(c) The Flame Trench 2021
Sheet: /CAN_XCVR_PL/ The Flame Trench Drawn by: Ben Cartwright Status: PROTOTYPE

File: CAN_XCVR.sch
Id: 9/11 Title: Singularity OBC - CAN Transceiver

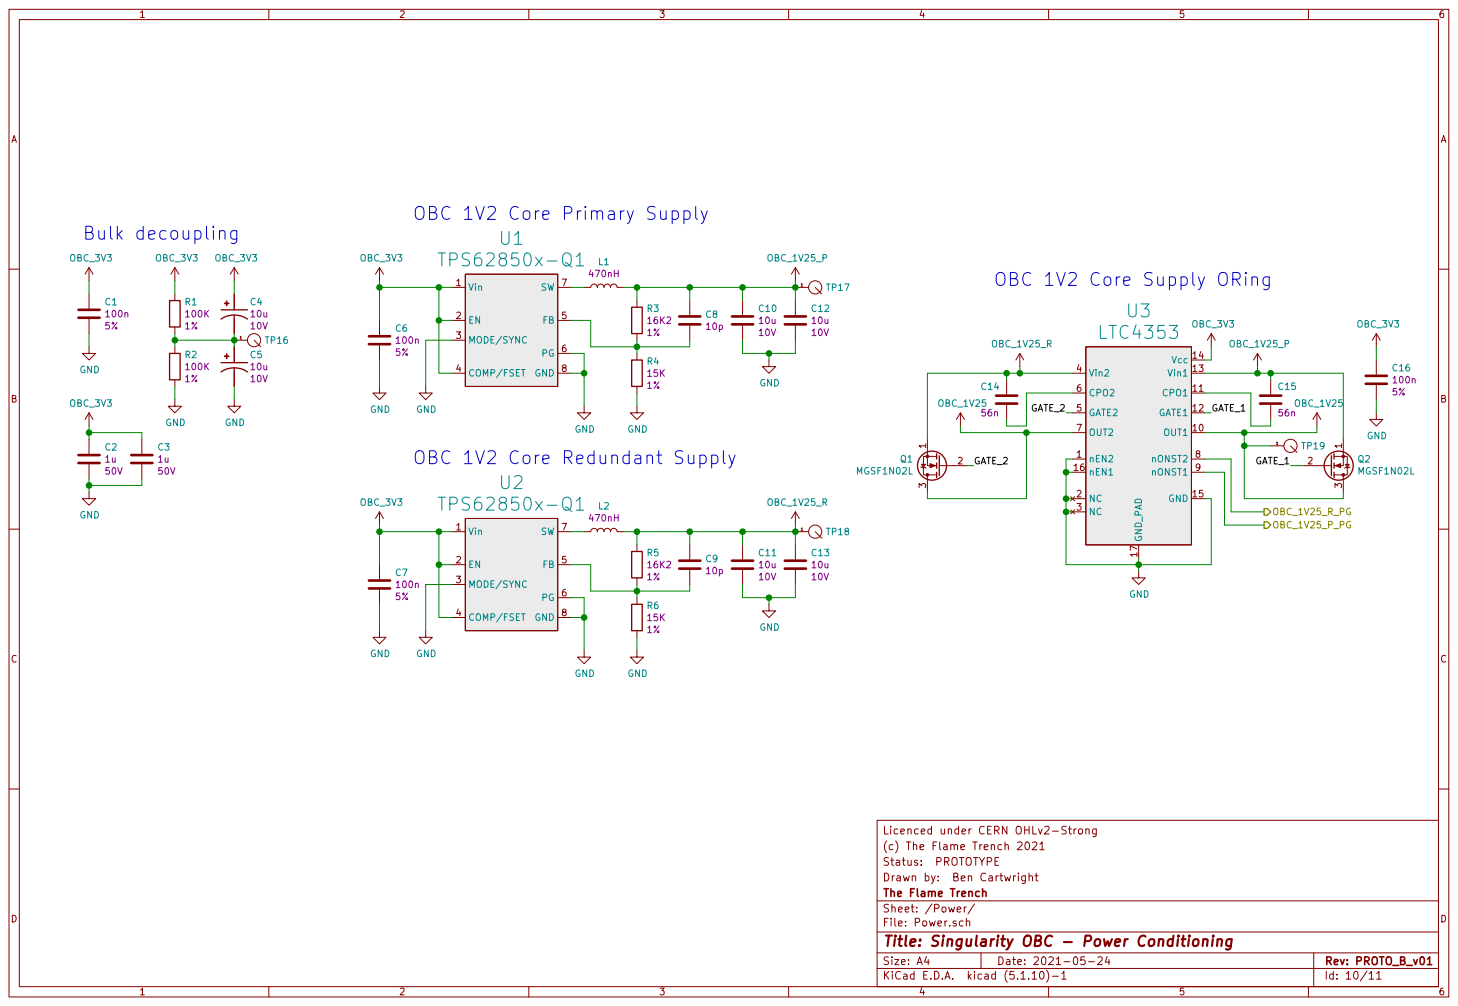
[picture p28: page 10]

OBC 1V2 Core Primary Supply

OBC 1V2 Core Supply ORing
LTC4353

OBC 1V2 Core Redundant Supply

(c) The Flame Trench 2021
File: Power.sch Sheet: /Power/ The Flame Trench Drawn by: Ben Cartwright Status: PROTOTYPE

Id: 10/11 Title: Singularity OBC - Power Conditioning


File: RTC_v2.sch Sheet: /RTC/
Id: 11/11 Title:

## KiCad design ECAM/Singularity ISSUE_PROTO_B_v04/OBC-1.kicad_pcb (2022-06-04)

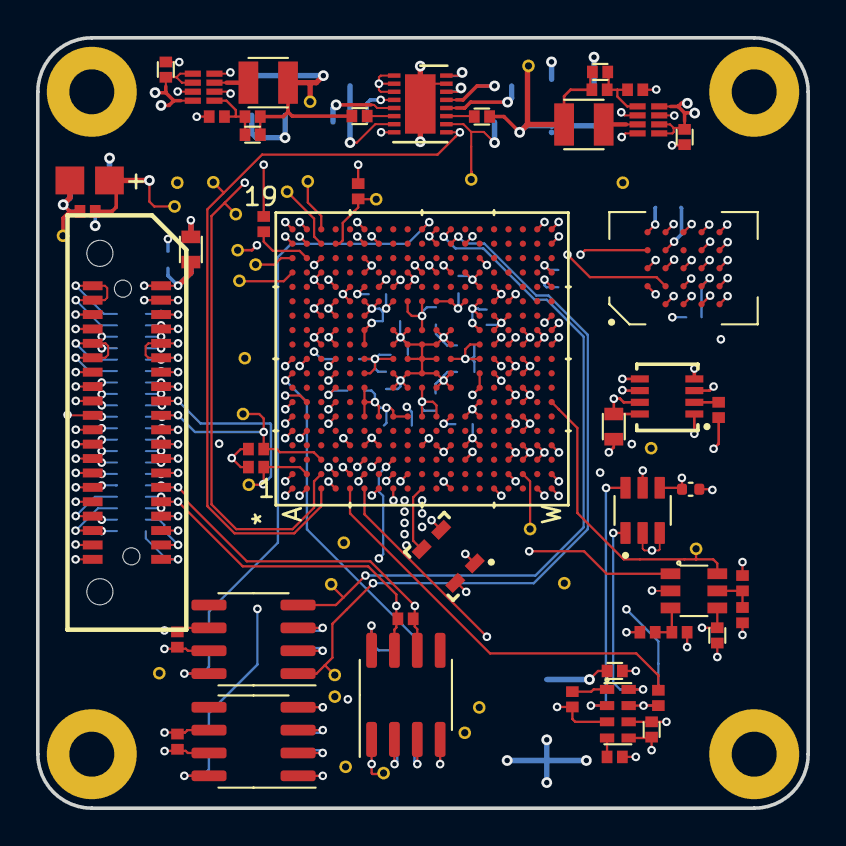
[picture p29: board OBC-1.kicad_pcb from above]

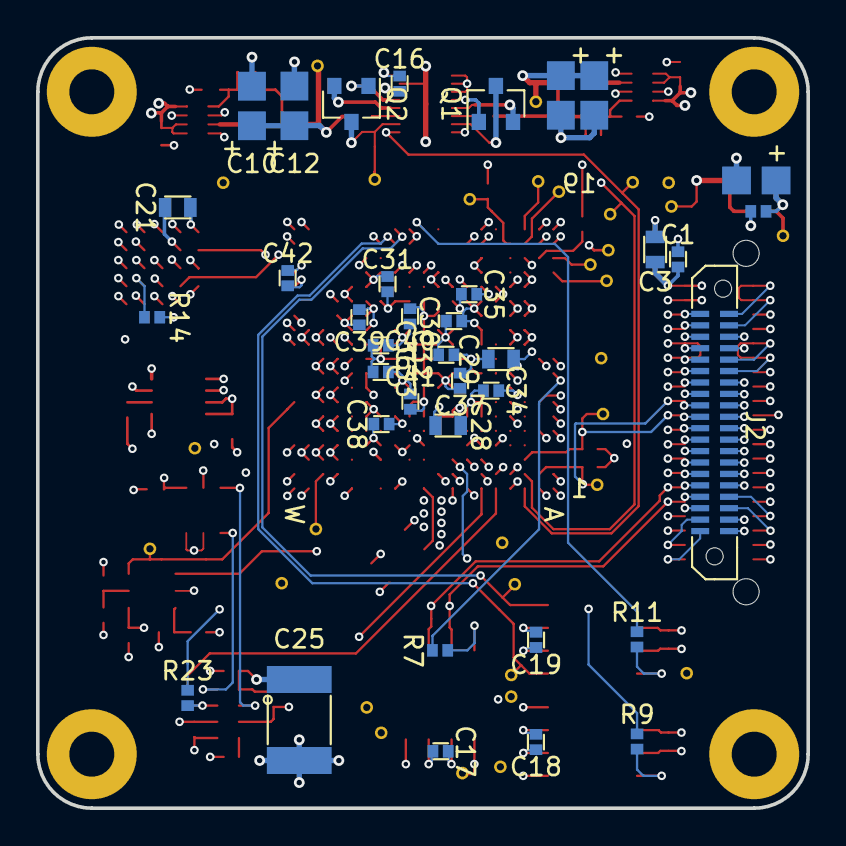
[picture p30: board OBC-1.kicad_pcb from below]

Board: 6 copper layers, 42.8 x 42.8 mm, 121 parts (37 on the bottom side), 76 nets.

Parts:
C1, C6, C7, C16, C17, C18, C19, C22, C23, C24, C30, C31, C32, C33, C34, C35, C36, C37, C38, C39, C40, C41, C42: 100n-10V-0402-5%-CER; 0402_CAP
C2, C3, C28, C29: 1u-10V-0603-10%-CER; 0603_CAP
C4, C5: 10u-10V-1206-10%-TANT; 1206_CAP_TANT
C8, C9: 10p-50V-0402-0.5p-CER; 0402_CAP
C10, C11, C12, C13: 10u-10V-0603-10%-CER; 1206_CAP_TANT
C14, C15: 56n-16V-0402-10%-CER; 0402_CAP
C20, C21: 100n-10V-0402-5%-CER; 0603_CAP
C25: 100uAH-1V8-4.4x3mm_LIon_batt; 1812_BATT
C26: 10n-10V-0402-5%-CER; C_0402_1005Metric
H1, H2, H3, H4: MountingHole_Pad; MountingHole_2.5mm_Pad
J1: ERM8-020-X; ERM8-020-XX.X-X-DV
J2: ERF6-020-X; ERF6-020-XX.X-X-DV-A-XX-K
L1, L2: 470nH-4A-20%; 2.5x2mm_I_SMD
Q1, Q2: MGSF1N02L; SOT-23
R1, R2: 100K-50V-0402-1%; 0402_RES
R3, R5: 16K2-50V-0402-1%; 0402_RES
R4, R6: 15K-50V-0402-1%; 0402_RES
R7, R9, R11, R25, R26: 10K-50V-0402-1%; 0402_RES
R8, R10, R12: 120R-50V-0402-1%; 0402_RES
R13, R14: 39R0-50V-0402-1%; 0402_RES
R15, R16, R21, R22, R23, R24: 0R-50V-0402; 0402_RES
R17, R18, R19, R20: 4K7-50V-0402-1%; 0402_RES
TP1, TP2, TP3, TP4, TP5, TP6, TP7, TP8, TP9, TP10, TP11, TP12, TP13, TP14, TP15, TP16, TP17, TP18, TP19, TP20, TP21, TP22, TP23, TP24, TP25, TP26, TP27, TP28, TP29, TP36, TP37: TEST-POINT; TP_0.4mmholesize_0.3mmring
U1, U2: TPS62850x-Q1; SOT-583
U3: LTC4353; DFN-16-1EP_3x4mm_P0.45mm_EP1.7x3.3mm
U4, U5, U6: SN65HVD230M-EP; SOIC-8_3.9x4.9mm_P1.27mm
U7: CY15B108QI
U8: S70FL01GS; BGA-24_5x5_6.0x8.0mm
U9: TPS3813K33-EP; SOT-236
U10: RV-3032-C7
U11: TMS5701227CZWTQQ1; ZWT337
U12: TMP100; SOT-23
X2: LFTCXO075797

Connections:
/CAN_XCVR_PL/CAN_H_PL: J1.16, R8.1, U4.7
/CAN_XCVR_PL/CAN_L_PL: J1.15, R8.2, U4.6
/CAN_XCVR_PL/CAN_PL_D: TP22.1, U4.1, U11.A10
/CAN_XCVR_PL/CAN_PL_R: TP24.1, U4.4, U11.B10
/CAN_XCVR_PL/CAN_PL_Rs: R7.1, U11.A9
/CAN_XCVR_R/CAN_H_PL: J1.19, J2.19, R10.1, U5.7
/CAN_XCVR_R/CAN_L_PL: J1.20, J2.20, R10.2, U5.6
/CAN_XCVR_R/CAN_PL_D: TP21.1, U5.1, U11.H2
/CAN_XCVR_R/CAN_PL_R: TP20.1, U5.4, U11.H1
/CAN_XCVR_R/CAN_PL_Rs: R9.1, U11.G1
/Connectors/ADS_nRST: J1.11, U11.M1
/Connectors/CAN_H_PA: J1.24, J2.24, R12.1, U6.7
/Connectors/CAN_L_PA: J1.23, J2.23, R12.2, U6.6
/Connectors/GPS_P1PPS: J1.29, U11.A6
/Connectors/GPS_RXD0: J1.31, U11.B7
/Connectors/GPS_STS: J1.28, U11.A5
/Connectors/GPS_TXD0: J1.32, U11.A7
/Connectors/GPS_nRST: J1.30, U11.B5
/FL_1/FL_1_CLK: U8.B2, U11.F18
/FL_1/FL_1_SI_IO0: U8.D3, U11.F19
/FL_1/FL_1_SO_IO1: R14.1, U11.G18
/FL_1/FL_1_nCS1: U8.C2, U11.F3
/FL_1/FL_1_nCS2: U8.A3, U11.G3
/FL_1/FL_1_nHOLD_IO3: U8.D4, U11.H3
/FL_1/FL_1_nRESET: U8.A4, U11.F2
/FRAM_1/FRAM_1_CIPO: R13.1, U11.D2
/FRAM_1/FRAM_1_CLK: U7.6, U11.E2
/FRAM_1/FRAM_1_COPI: U7.5, U11.D1
/FRAM_1/FRAM_1_nCS: U7.1, U11.N3
/Power/GATE_1: Q2.2, U3.12
/Power/GATE_2: Q1.2, U3.5
/Power/OBC_1V25_P_PG: TP36.1, U3.9, U11.C1
/Power/OBC_1V25_R_PG: TP37.1, U3.8, U11.C2
/RTC/OBC_I2C_SCL: J1.10, R20.2, TP29.1, U10.8, U11.C3, U12.1
/RTC/OBC_I2C_SDA: J1.9, R19.2, TP28.1, U10.2, U11.B2, U12.6
/RTC/RTC_CLKOUT: R23.2, R24.2, U10.7
/RTC/RTC_nINT: R26.2, U10.3, U11.F1
/Supervisor/SPVSR_PET: U9.1, U11.J2
/Supervisor/SPVSR_nRST: TP27.1, U9.6, U11.W7
/Supervisor/WDR: R21.2, R22.1, U9.5
/Supervisor/WDT: R15.2, R16.1, U9.3
/TMS570_uC/CAN_PA_D: TP25.1, U6.1, U11.M18
/TMS570_uC/CAN_PA_R: TP23.1, U6.4, U11.M19
/TMS570_uC/CAN_PA_Rs: R11.1, U11.K19
/TMS570_uC/JTAG_RTCK: TP1.1, U11.A16
/TMS570_uC/JTAG_TCK: TP5.1, U11.B18
/TMS570_uC/JTAG_TDI: TP2.1, U11.A17
/TMS570_uC/JTAG_TDO: TP6.1, U11.C18
/TMS570_uC/JTAG_TEST: TP3.1, U11.U2
/TMS570_uC/JTAG_TMS: TP7.1, U11.C19
/TMS570_uC/JTAG_nTRST: R17.1, TP4.1, U11.D18
/TMS570_uC/uC_OSC_IN: U11.K1, X2.3
/TMS570_uC/uC_nRST: R18.1, U11.B17
GND: C1.2, C2.2, C3.2, C5.2, C6.2, C7.2, C10.2, C11.2, C12.2, C13.2, C16.2, C17.2, C18.2, C19.2, C20.2, C21.2, C22.2, C23.2, C24.2, C25.2, C26.2, C28.2, C29.2, C30.2, C31.2, C32.2, C33.2, C34.2, C35.2, C36.2, C37.2, C38.2, C39.2, C40.2, C41.2, C42.2, H1.1, H2.1, H3.1, H4.1, J1.3, J1.4, J1.5, J1.6, J1.7, J1.8, J1.12, J1.13, J1.14, J1.17, J1.18, J1.21, J1.22, J1.25, J1.26, J1.27, J1.33, J1.34, J1.37, J1.38, J2.1, J2.2, J2.3, J2.4, J2.5, J2.6, J2.7, J2.8, J2.9, J2.10, J2.11, J2.12, J2.13, J2.14, J2.15, J2.16, J2.17, J2.18, J2.21, J2.22, J2.25, J2.26, J2.27, J2.28, J2.29, J2.30, J2.31, J2.32, J2.33, J2.34, J2.37, J2.38, R2.2, R4.2, R6.2, R16.2, R22.2, TP8.1, TP9.1, TP10.1, TP11.1, TP12.1, TP13.1, TP14.1, TP15.1, U1.3, U1.6, U1.8, U2.3, U2.6, U2.8, U3.1, U3.2, U3.3, U3.15, U3.16, U3.17, U4.2, U5.2, U6.2, U7.4, U8.A2, U8.A5, U8.B1, U8.B3, U8.B5, U8.C1, U8.C3, U8.C5, U8.D1, U8.D5, U8.E1, U8.E2, U8.E3, U8.E4, U8.E5, U9.2, U10.5, U11.A1, U11.A2, U11.A18, U11.A19, U11.B1, U11.B19, U11.C11, U11.C12, U11.C13, U11.C14, U11.C15, U11.C16, U11.C17, U11.D6, U11.D7, U11.D8, U11.D9, U11.D10, U11.D11, U11.D12, U11.D13, U11.D14, U11.D15, U11.E4, U11.E14, U11.E15, U11.F4, U11.F15, U11.F16, U11.F17, U11.G4, U11.G15, U11.H8, U11.H9, U11.H11, U11.H12, U11.H15, U11.J8, U11.J9, U11.J10, U11.J11, U11.J12, U11.J15, U11.J16, U11.K4, U11.K9, U11.K10, U11.K11, U11.K16, U11.L4, U11.L8, U11.L9, U11.L10, U11.L11, U11.L12, U11.L16, U11.L18, U11.L19, U11.M4, U11.M8, U11.M9, U11.M11, U11.M12, U11.M16, U11.N4, U11.N16, U11.N18, U11.P4, U11.P15, U11.P16, U11.P17, U11.R1, U11.R10, U11.R11, U11.R12, U11.R13, U11.R14, U11.R15, U11.T2, U11.T3, U11.T4, U11.T5, U11.T6, U11.T7, U11.T8, U11.T9, U11.T10, U11.T11, U11.T13, U11.T14, U11.U3, U11.U4, U11.U5, U11.U6, U11.U7, U11.U8, U11.U9, U11.U10, U11.U11, U11.U12, U11.V1, U11.V3, U11.V4, U11.V11, U11.V12, U11.V19, U11.W1, U11.W2, U11.W4, U11.W11, U11.W12, U11.W13, U11.W16, U11.W18, U11.W19, U12.2, U12.3, U12.5, X2.1, X2.2
unnamed: C4.2, C5.1, R1.2, R2.1, TP16.1
unnamed: C8.2, R3.2, R4.1, U1.5
unnamed: C9.2, R5.2, R6.1, U2.5
unnamed: C14.2, U3.6
unnamed: C15.2, U3.11
unnamed: L1.1, U1.7
unnamed: L2.1, U2.7
unnamed: R7.2, U4.8
unnamed: R9.2, U5.8
unnamed: R11.2, U6.8
unnamed: R13.2, U7.2
unnamed: R14.2, U8.D2
unnamed: R23.1, U11.R9
unnamed: R24.1, U11.E1
unnamed: R25.2, U10.4
OBC_1V25: C29.1, C32.1, C33.1, C36.1, C37.1, C40.1, C41.1, Q1.3, Q2.3, TP19.1, U3.7, U3.10, U11.F9, U11.F10, U11.H10, U11.J14, U11.K6, U11.K8, U11.K12, U11.K14, U11.L6, U11.M10, U11.P10, U11.P11
OBC_1V25_P: C8.1, C10.1, C12.1, C15.1, L1.2, Q2.1, R3.1, TP17.1, U3.13
OBC_1V25_R: C9.1, C11.1, C13.1, C14.1, L2.2, Q1.1, R5.1, TP18.1, U3.4
OBC_3V3: C1.1, C2.1, C3.1, C4.1, C6.1, C7.1, C16.1, C17.1, C18.1, C19.1, C20.1, C21.1, C22.1, C23.1, C26.1, C28.1, C30.1, C31.1, C34.1, C35.1, C38.1, C39.1, C42.1, J1.1, J1.2, R1.1, R15.1, R17.2, R18.2, R19.1, R20.1, R21.1, R25.1, TP26.1, U1.1, U1.2, U1.4, U2.1, U2.2, U2.4, U3.14, U4.3, U5.3, U6.3, U7.3, U7.7, U7.8, U8.B4, U9.4, U10.6, U11.F6, U11.F7, U11.F8, U11.F11, U11.F12, U11.F13, U11.F14, U11.G6, U11.G14, U11.H6, U11.H14, U11.J6, U11.L14, U11.M6, U11.M14, U11.N6, U11.N14, U11.P6, U11.P7, U11.P8, U11.P9, U11.P12, U11.P13, U11.P14, U11.W15, U12.4, X2.4
OBC_RTC_Vbackup: C24.1, C25.1, R26.1, U10.1
PAYLOAD_3V3: J1.35, J1.36, J2.35, J2.36
PAYLOAD_5V: J1.39, J1.40, J2.39, J2.40

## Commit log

2021-03-12 First commit to online source, schematic status ISSUE_PROTO_A ready for footprint and PCB dev
    [CAN_XCVR.sch, Connectors.sch, FL_1Gbit.sch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]
2021-03-24 Minor schematic information updates
    [CAN_XCVR.sch, Connectors.sch, FL_1Gbit.sch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]
2021-03-24 added PCB outline, fixed some mispositioning in the schematic, removed incorrect footprint assignment from U7
    [CAN_XCVR.sch, Connectors.sch, FL_1Gbit.sch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]
2021-03-24 addded prelim HTML BoM files
    [OBC-1.kicad_pcb]
2021-03-28 corrected labelling issue on top level schematic
    [OBC-1.sch]
2021-03-29 set up PCB stackup and routing design rules, began power planing and power breakouts for the TMS570
    [OBC-1.kicad_pcb]
2021-03-30 added extra decoupling cap for VCCAD and completed initial routing of TMS570 power breakout and decoupling
    [OBC-1.kicad_pcb, TMS570_uC.sch]
2021-03-30 replaced power ORing MOSFETs with lower Rds SOT-23 package
    [OBC-1.kicad_pcb, Power.sch, TMS570_uC.sch]
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2021-03-30 Add power budget spreadsheet
    [Power Budget.xlsx]
2021-03-30 schematic updated with new power symbols for OBC_1V25
    [OBC-1.sch, Power.sch, TMS570_uC.sch]
2021-03-30 changed resistor dividers in the power section to supply 1.25V to TMS570 core
    [Power.sch]
2021-03-30 Add more calculations to power budget
    [Power Budget.xlsx]
2021-03-31 annoted new regulator Vout set resistors
    [Power.sch, TMS570_uC.sch]
2021-03-31 assigned testpoint and ERF6 footprints
    [Connectors.sch, OBC-1.sch, Power.sch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]
2021-03-31 corrected heirarchical label naming after 1.25v power change
    [TMS570_uC.sch]
2021-03-31 added new footprints to layout in prep for locating connector positions
    [OBC-1.kicad_pcb]
2021-03-31 finalised connector position, updated testpoint footprint assingment. SMPS footprint netlist has a bug that will hopefully be fixed when it has a valid footprint
    [OBC-1.kicad_pcb, OBC-1.sch, Power.sch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]
2021-03-31 fixed incorrect footprint assignment to U1 and U2
    [OBC-1.kicad_pcb, Power.sch, TMS570_uC.sch]
2021-03-31 connectors broken out
    [OBC-1.kicad_pcb]
2021-03-31 updates to CAN power trace routing and initial CAN differential rail routing
    [CAN_XCVR.sch, Connectors.sch, OBC-1.kicad_pcb]
2021-04-01 signals broken out from TMS570
    [OBC-1.kicad_pcb]
2021-04-01 added board level bulk decoupling
    [CAN_XCVR.sch, OBC-1.kicad_pcb, Power.sch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]
2021-04-01 first power supply laid out
    [OBC-1.kicad_pcb]
2021-04-01 updated passive footprints, fixed errors, re-laid out CAN xcvrs
    [CAN_XCVR.sch, Connectors.sch, FL_1Gbit.sch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]
2021-04-01 initial layout of 2nd power supply done, 3V3 plane routing to the supply inputs needs work, currently too broken up by ground vias
    [OBC-1.kicad_pcb]
2021-04-01 added testpoints to 2nd supply, positioned early floorplan for ORing diode controller, needs work - gates are on wrong sides - need to switch supply sides
    [OBC-1.kicad_pcb]
2021-04-01 cleanup save of sch
    [Power.sch]
2021-04-01 updated CAN xcvr positions
    [OBC-1.kicad_pcb]
2021-04-01 fixed wonky payload CAN bus routing
    [CAN_XCVR.sch, Connectors.sch, OBC-1.kicad_pcb]
2021-04-02 progressed power supply layout, added 3D models to footprints
    [CAN_XCVR.sch, OBC-1.kicad_pcb, Power.sch]
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2021-04-02 initial supervisor layout, needs XTAL adding
    [OBC-1.kicad_pcb, Supervisor_RTC_FRAM.sch, TMS570_uC.sch]
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2021-04-02 initial SDRAM positioning, need to floorplan remainder of memory ICs
    [OBC-1.kicad_pcb, SDRAM_128Mbit.sch]
2021-04-02 fixed bus netlisting issue - labelling was incorrectly formatted
    [OBC-1.kicad_pcb, OBC-1.sch, SDRAM_128Mbit.sch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]
2021-04-02 removed SDRAM to simplify initial design
    [CAN_XCVR.sch, Connectors.sch, FL_1Gbit.sch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]
2021-04-02 fixed typo in GPS net label
    [OBC-1.kicad_pcb, OBC-1.sch, TMS570_uC.sch]
2021-04-02 fixed typo in README, added flash chip for floorplanning, added JTAG testpoints for pogo pinning
    [FL_1Gbit.sch, OBC-1.kicad_pcb, Supervisor_RTC_FRAM.sch]
2021-04-02 initial routing of flash chip
    [OBC-1.kicad_pcb]
2021-04-02 updated flash chip breakout and bus routing to neaten and simplify, keeping to one layer
    [OBC-1.kicad_pcb]
2021-04-02 added pullup resistors for I2C, reset, etc. routed PG lines
    [OBC-1.kicad_pcb]
2021-04-02 rerouted some power to make routing supervisor comms bus easier
    [OBC-1.kicad_pcb]
2021-04-02 routed supervisor SPI and IO ports
    [OBC-1.kicad_pcb]
2021-04-02 fixed 3V3 plane vertex
    [OBC-1.kicad_pcb]
2021-04-02 payload CAN bus routed
    [OBC-1.kicad_pcb]
2021-04-03 moved some of the TMS570 grounding vias to make room for updated 1V25 power plane
    [OBC-1.kicad_pcb]
2021-04-03 further prep for TMS570 power plane routing
    [OBC-1.kicad_pcb]
2021-04-03 added new power planes for TMS570
    [OBC-1.kicad_pcb]
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2021-04-03 temporarily made all connector grounding vias blind to only one ground plane, will revert some once connector is fully broken out and routed to keep local plane balance
    [Connectors.sch, OBC-1.kicad_pcb]
2021-04-03 GPS UART and IO routed to connector
    [OBC-1.kicad_pcb]
2021-04-03 increased signal separation of power-good traces from I2C section
    [OBC-1.kicad_pcb]
2021-04-03 fixed unnecessary trace necking under BGA component
    [OBC-1.kicad_pcb]
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2021-05-08 Updated KiCAD to 5.1.10 and restructured repo files
    [CAN_XCVR.sch, Connectors.sch, FL_1Gbit.sch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]
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2021-05-24 updated schematic with FRAM footprint link
    [FRAM_8Mbit.sch]
2021-05-24 added FRAM to PCB layout
    [OBC-1.kicad_pcb]
2021-05-24 added ground test points, adjusted trace width on RTC XTAL
    [OBC-1.kicad_pcb]
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2021-05-24 updated uC XTAL footprint assignment
    [TMS570_uC.sch]
2021-05-24 added uC XTAL, routed ground stitching and power plane
    [OBC-1.kicad_pcb]
2021-05-24 updated schematic with release date, plotted updated pdf
    [CAN_XCVR.sch, Connectors.sch, FL_1Gbit.sch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]
2021-05-24 added new supervisor circuit to schematic
    [CAN_XCVR.sch, Connectors.sch, FL_1Gbit.sch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]
2021-05-24 added RTC schematic, fixed ADS_nRST pin not driven by TMS570
    [CAN_XCVR.sch, Connectors.sch, FL_1Gbit.sch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]
2021-05-24 fixed ADS_nRST pin not driven
    [CAN_XCVR.sch, TMS570_uC.sch]
2021-05-24 revised schematic to PROTO_A_v02
    [CAN_XCVR.sch, Connectors.sch, FL_1Gbit.sch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]
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2021-05-24 file catchup - RTCv2.sch and ISSUE_PROTO_B pdfs
    [RTC_v2.sch]
2021-05-24 plotted issue proto_A_v02 schematic pdf
2021-05-24 updated PCB layout for Issue B supervisor/RTC circuitry
    [OBC-1.kicad_pcb, Power.sch, RTC_v2.sch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]
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2021-05-24 updated Issue_proto_B schematic plot
    [OBC-1.sch]
2021-05-29 initial commit, power test points linked to heirarchy
    [CAN_XCVR.sch, Connectors.sch, FL_1Gbit.sch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]
2021-05-29 set up test points for TSM570 schematic
    [CAN_XCVR.sch, Connectors.sch, FL_1Gbit.sch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]
2021-05-29 cleaned up modules with no current testpoints
    [Connectors.sch, OBC-1.sch, Power.sch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]
2021-05-29 updated RFC connector on BoN to ERF8 for bottom layer mounting
    [Connectors.sch]
2021-06-03 file cleanup, .attributes update
    [OBC-1.sch, RTC.sch]
2021-06-05 Fix power budget math
    [Power Budget.xlsx]
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2021-06-05 added OBC_1V25_P/R_PG net test points, updated TP ref des
    [CAN_XCVR.sch, Connectors.sch, FL_1Gbit.sch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]
2021-06-05 added Power Good testpoints to 1V25_P/R_PG rails, removed unnecessary TP35 from power schematic
    [OBC-1.kicad_pcb, Power.sch]
2021-06-05 updated title blocks and testpoint/connector passthroughs
    [Connectors.sch, OBC-1.sch, Power.sch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]
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2021-06-05 updating PCB with current proto_B test point locations
    [OBC-1.kicad_pcb]
2021-06-05 further PCB update to locate test points with current issue B PCB
    [OBC-1.kicad_pcb]
2021-06-05 updated schematic dates and titles
    [CAN_XCVR.sch, Connectors.sch, FL_1Gbit.sch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]
2021-06-05 plotted issue_Proto_B_v02 schematic
2021-06-05 updated TP35 to TP19 to match base computer refdes in BoN
    [Power.sch]
2022-06-04 migrated to KiCAD v6. For now, old v5 files remain as legacy. Please only use v6 from now on
    [CAN_XCVR.kicad_sch, Connectors.kicad_sch, FL_1Gbit.kicad_sch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]
2022-06-04 updated BoN directory to KiCAD v6
    [Connectors.kicad_sch, OBC-1.kicad_sch, OBC-1_v04.kicad_pcb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]
2022-06-04 added PCB from most up to date IssB_v04, needs components removing and TP refdes checking as in Issue27
    [OBC-1_v04.kicad_pcb]

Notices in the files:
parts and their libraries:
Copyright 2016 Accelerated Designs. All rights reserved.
